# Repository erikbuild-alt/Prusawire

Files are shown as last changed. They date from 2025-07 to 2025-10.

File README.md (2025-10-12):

# Prusawire 2025.B1

Render

A wholly unofficial Prusa MK3 and MK4 total conversion mod, from Positron's April Fools of 2025.

## About

> Nomad of Positron3D came up with this idea shortly after completing their Switchwire build. The idea started as a quick design exercise, to try and convert a Prusa MK4S frame into a Switchwire, using everything left over from a CORE One Upgrade.
>
> As the first iteration wrapped up, I took interest in the project, and decided to take this April Fools joke one step further and build it into a reliable machine.
>
> After months of hard work, please enjoy the build ❤
> 
> [-@ellafoxo](https://www.printables.com/@ellafoxo)

## Who This Printer is For

Pick one of the following:

 - You have an old MK3, MK3S, or MK3S+, and you want to teach an old dog new tricks and are on a budget
 - You upgraded from MK4S to a Core ONE, and have a leftover frame. You are okay spending money on building a new printer with that hardware.

Additionally, the following says this printer is for you: 

 - You want to take your first steps into RepRap beyond Prusa, and Voron is an exciting route.
 - You are comfortable working from a CAD file as your build guide
 - You respect the Frankenstein-y nature of this April Fools joke printer

## Want to Support the Project?

First of all, thank you! Development costs have been mostly self-funded, with filament sponsored by Levendigs, and LDO Motors for providing the funds for the Prusa MK4 frame.

 - Buy me a Ko-Fi
 - Support Positron3D to fund future endeavors

## 2025 - Beta 1

This printer is in active development. Please check back regularly for bug fixes and configuration updates!

## Build Volume

X: 250mm
Y: 210mm
Z: 185mm

## Bill of Materials

[Prusawire 2025.B1 Bill of Materials](BOM/BOM_2025-B1.md)

## Technical Support

Prusawire, technically, does not count as a Voron Switchwire. We ask you kindly not to nag the Voron Design team for technical support.

Instead, please [join the Positron3D Discord](https://discord.com/invite/positron) for support with your build, and maybe share your progress over there too.

## Serial Numbers

We are accepting serials over on the [Positron 3D Discord](https://discord.com/invite/positron). Please submit your request to the #prusawire-serial-request channel over there. 

## Upgrading the Einsy Rambo to Klipper - Read this

Installing Klipper on the Einsy Rambo board is possible, with extra steps. Follow the guide [published by the awesome folks at MyRigs3D](https://myrigs3d.com/blogs/infos/revive-your-prusa-mk3s-with-klipper-1-5-flash-bootloader)! We recommend Method 2.

**Note:** Some users have reported problems using `avrdude` with the latest Raspberry Pi OS version (bookworm). If you experience error messages from avrdude complaining about gpio ports being busy, please try using the bullseye version of Raspberry Pi OS instead, available as "Raspberry Pi OS (Legacy)" in Raspberry Pi Imager.

## Klipper Configuration Files

The most up–to–date Klipper configuration files for setting up or updating the Prusawire are in our [config repository](https://github.com/Positron3D/prusawire-klipper-config).

## Credits 

Many thanks to all the awesome people and companies that have made this possible. Notably:

 - Prusa Research - Cheers, Josef and the team for the MK3/4 platform on which this was built upon!
 - Voron Design - Switchwire
 - Positron 3D Team - Too many to name, you know who you are <3
   - Early development team:
     - Nomad's Galaxy
     - Koosh
     - Birb
 - Jason @ LDO Motors - Part sponsorship
 - Levendigs - Part sponsorship 
 - Early access testers:-
    - Killa_Prints
    - LinksLab
    - Safe
    - Silicon
    - TheNexusAvenger
    - torsten

## Extra Credits for Existing Printed Parts

See the collection for the most up to date! To name them:

 - Printable M3 T-Nuts for 3030 Extrusion, by Kapplion
 - Stealthburner umbilical strain relief, by nagelwerkstatt

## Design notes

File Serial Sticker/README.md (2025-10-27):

Prusawire Serial

Custom serial sticker for Prusawire. Designed for 24 mm tape. Files include a printable cutting stencil.

Brother TZe-M951 Black/Matt Silver tape is tested.

Template files are available as Affinity Designer 2 and Inkscape files.
Used fonts are from [Google Fonts](https://fonts.google.com/specimen/Play). Play in regular and bold.

[Inkscape](https://inkscape.org)

[WEEE symbol](https://europa.eu/youreurope/business/product-requirements/labels-markings/weee-label/index_en.htm)

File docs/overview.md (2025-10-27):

---
layout: default
title: Overview
nav_order: 2
---

# Overview

Welcome to the Prusawire documentation.

## Overview

- [Frequently Asked Questions](faq.html)
- [Bill of Materials](bom.html): Links to all current BOM information.
- [Assembly Manual](assembly-manual.html): Links to the latest Prusawire Assembly Manual PDF.

## Hardware

- [Gantry Deracking](hardware/gantry-deracking.html): How to derack the gantry for smooth and accurate motion.
- [XZ Belt Installation and Tensioning](hardware/xz-belt.html): How to install the main CoreXZ Motion Belts.
- [Y Belt Installation and Tensioning](hardware/y-belt.html): How to install the Y Motion Belt.

## Software
 - [Software Installation Overview](software/index.html)

## Tuning and Calibration
 - [Tuning and Calibration](tuning-calibration/index.html)

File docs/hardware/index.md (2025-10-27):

---
layout: default
title: Hardware Overview
has_children: true
nav_order: 6
---

# Hardware Overview

The official Assembly Manual (along with the Fusion CAD Link) should be your guide for assembly.  There are, of course, a few more complicated procedures which we have documented in detail here:

- Gantry Deracking
- XZ Belt
- Y Belt

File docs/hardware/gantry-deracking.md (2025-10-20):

---
layout: default
title: Gantry Deracking
parent: Hardware Overview
nav_order: 1
---

# Gantry Deracking
{: .no_toc}

<details open markdown="block">
  <summary>
    Table of contents
  </summary>
  {: .text-delta }
- TOC
{:toc}
</details>

**Current Compatibility:** *Prusawire - Beta 1*

## Overview
The gantry de-racking procedure is critical to ensure smooth motion in X and Z.  The general idea is to loosen certain screws on the gantry, bump the bottom of the gantry against the X and Z motor joints to align, and tighten the screws.

## Prerequisites
- Confirm your frame geometry is square: [Frame Assembly - Geometry Check](https://help.prusa3d.com/guide/2-frame-assembly_427481#427929)
- The following should be assembled already:
	- Frame
	- Z-Axis
	- X-Gantry with toolhead mount
- You should be ready to belt both the X and Z axis.

## Instructions
1. Remove the **toolhead** from the **carriage mount** (if currently installed).
	1. For Stealthburner, see the Stealthburner assembly manual for instructions.
2. Remove the **bed**, **y-carriage**, and **y-rods** completely off the printer (if currently installed).
3. Remove the **bumper block** and **door puller block** from the back of the gantry (if currently installed).

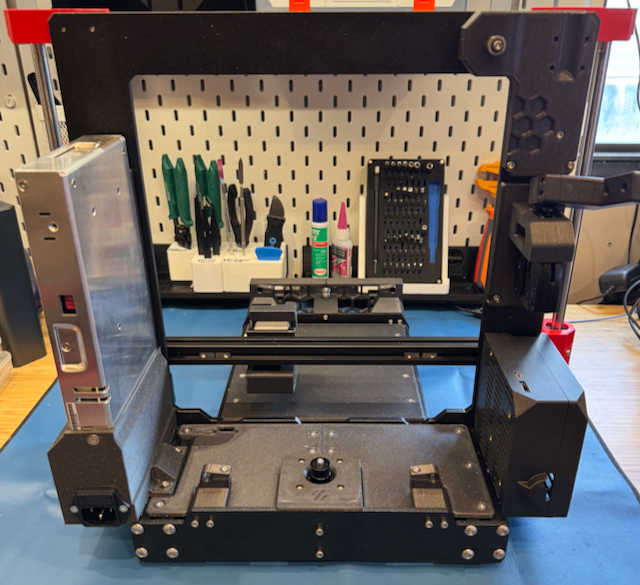
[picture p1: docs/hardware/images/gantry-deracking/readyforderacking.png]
	

4. Remove the **top left idler assembly** and **top right idler assembly** loosening the M3 SHCS on each.  
	1. *TIP: A small piece of tape on the top and bottom of the assembly can be used to help keep the bearing stack together.*

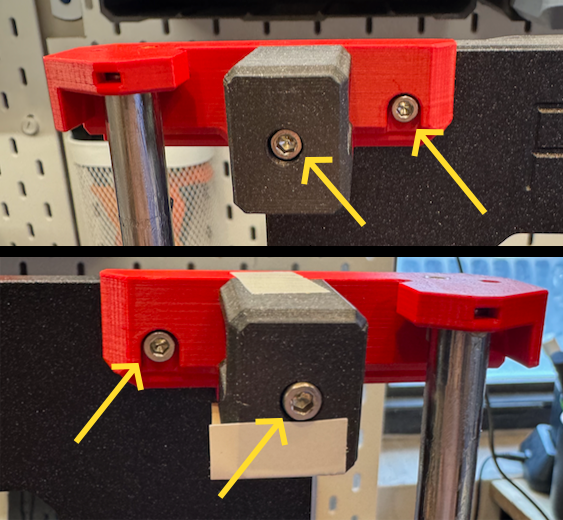
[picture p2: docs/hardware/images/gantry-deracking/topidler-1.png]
	
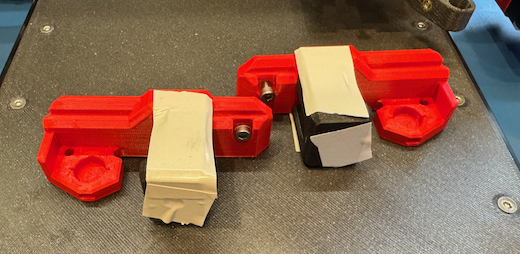
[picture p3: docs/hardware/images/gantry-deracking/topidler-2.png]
	

5. Remove the **x-gantry assembly from the printer** by lifting it up off the z-axis rods.
6. Loosen all six **M5 BHCS** from each side of the x-gantry assembly.

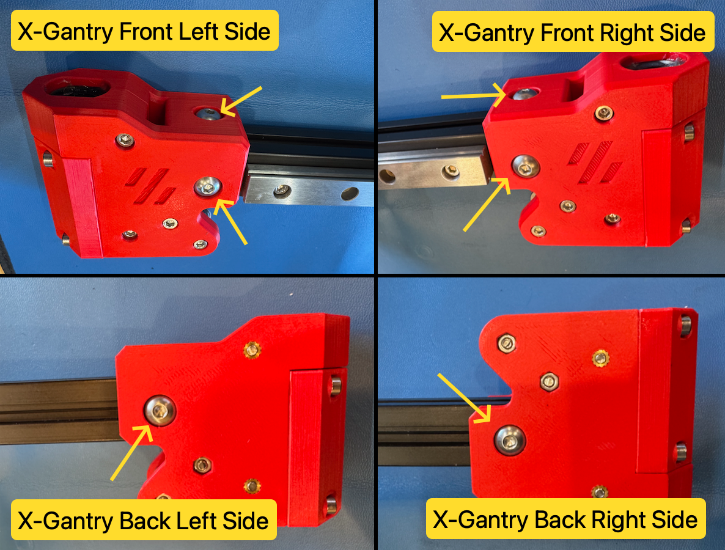
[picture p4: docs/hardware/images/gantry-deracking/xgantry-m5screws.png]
	

7. Ensure each end of the 2020 extrusion is seated ALL the way into the printed parts.
8. Re-install the **x-gantry assembly** onto the printer by sliding it onto the z-axis rods from the top.
9. Move the **x-gantry assembly** up and down a few times to allow parts to settle.
10. Lower the **x-gantry assembly** until it bumps against the X and Z motor mounts.

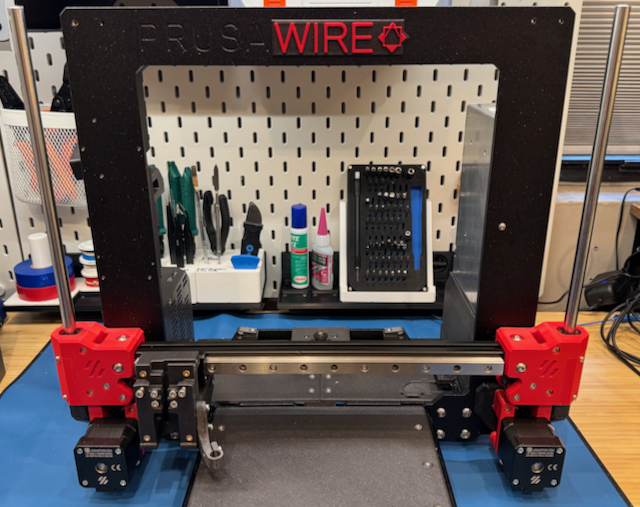
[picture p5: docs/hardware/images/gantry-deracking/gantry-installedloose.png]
	

11. Tighten the two top M5 BHCS on the x-gantry assembly, followed by the two front M5 BHCS.

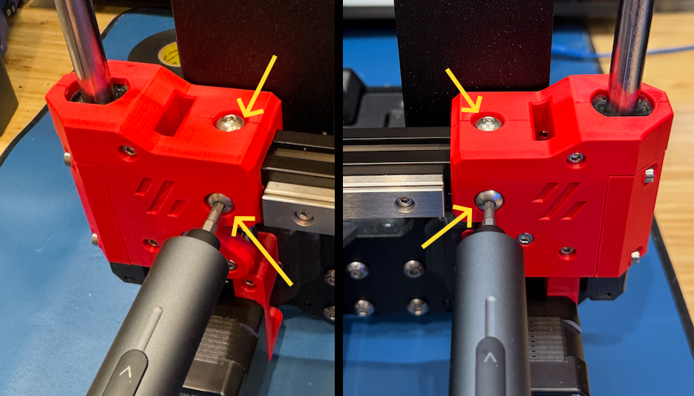
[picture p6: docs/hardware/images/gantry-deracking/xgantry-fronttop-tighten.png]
	

12. Raise the **x-gantry assembly** up to the top just high enough to be able to tighten the rear two M5 BHCS.

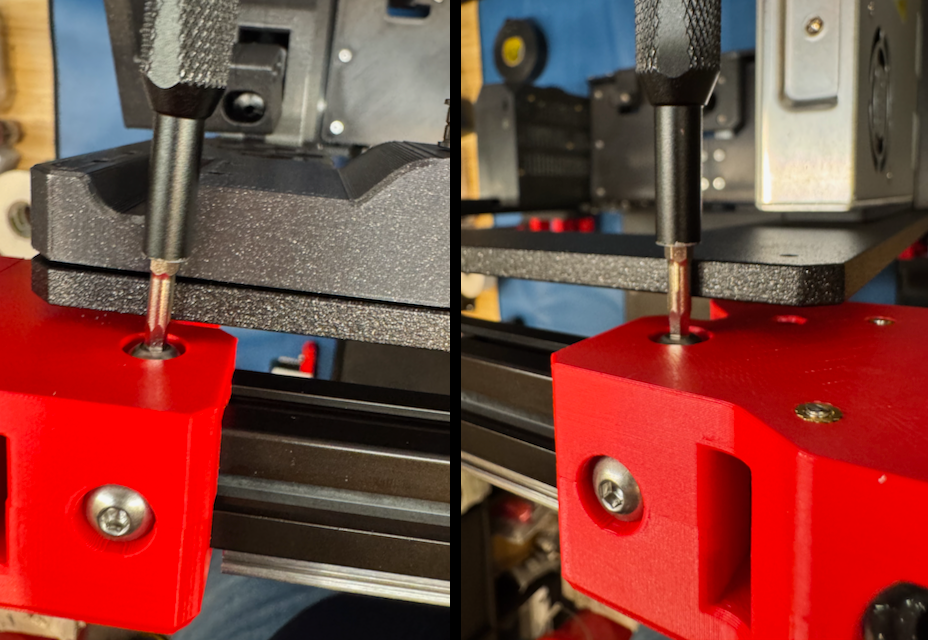
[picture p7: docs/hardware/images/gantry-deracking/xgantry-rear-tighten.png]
	

13. Lower the **x-gantry assembly** back down to the bottom.
14. Re-install the **top left idler assembly** and **top right idler assembly** by tightening the two M3 SHCS on each.
15. Re-install the **bumper block** and **door puller block** on the rear of the gantry.
16. Move the gantry up and down.  You shouldn't feel any resistance.

	

	1. When the gantry bumps the top of the frame, it should bump equally on both sides.

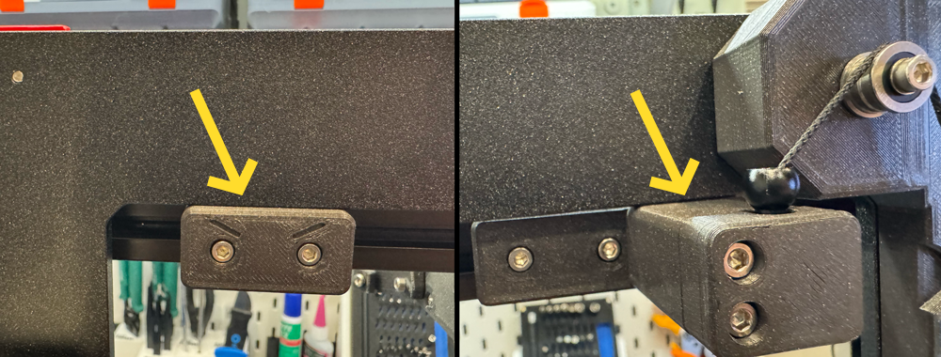
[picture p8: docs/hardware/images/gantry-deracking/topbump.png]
	

	2. When the gantry bumps the bottom (X motor mount and Z motor mount), it should bump equally on both sides.

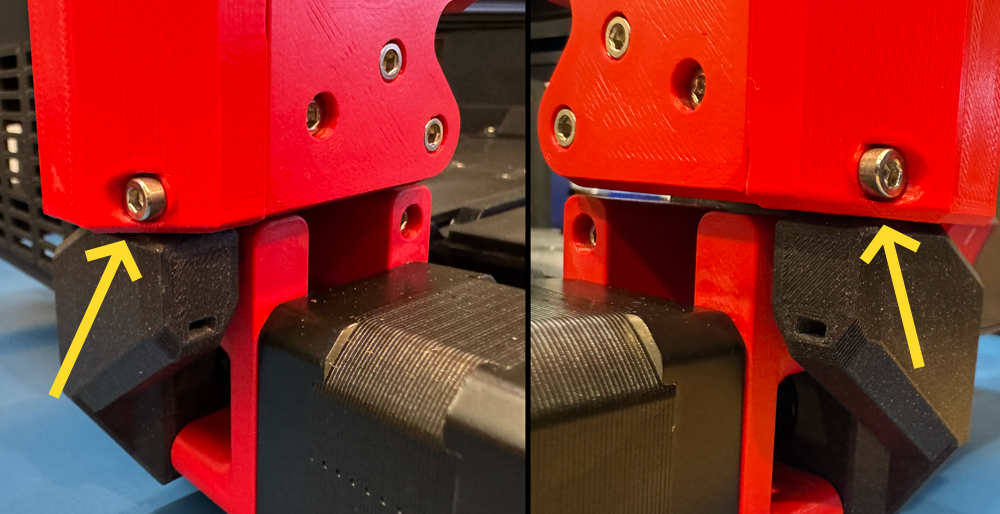
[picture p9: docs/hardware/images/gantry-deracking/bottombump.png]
	

17. Check for any gantry racking a final time after installing XZ belts (and prior to installation of Y-axis).  Adjust front/top M5 screws if needed.

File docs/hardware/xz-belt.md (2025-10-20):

---
layout: default
title: XZ Belt Installation and Tensioning
parent: Hardware Overview
nav_order: 2
---

# XZ Belt Installation and Tensioning
{: .no_toc}

<details open markdown="block">
  <summary>
    Table of contents
  </summary>
  {: .text-delta }
- TOC
{:toc}
</details>

**Compatibility:** *Prusawire - Beta 1*

## Overview
The X and Z belts must be installed and tensioned properly to ensure smooth and accurate gantry motion.

**Important notes:**
- Extra belt length has been specified in the BOM; it is expected to have some leftover belt afterwards.
- Match your belt lengths before assembling the printer!
- When inserting the belt clips, there should be an equal number of teeth sticking out of the ends.
- **DO NOT cut your belts** until you are 1000% certain you have done it correctly.  It's okay to leave a little extra length hanging out the back of the toolhead carriage until final assembly and validation.

## Prerequisites
- Complete the Gantry Deracking procedure.
- Remove the **toolhead** from the **carriage mount** (if currently installed).
	1. For Stealthburner, see the Stealthburner assembly manual for instructions.
- (Optional, but highly recommended) Print and assemble the GT2 Belt Runner to easily and perfectly match your belt lengths: [Belt Runner - GT2 Belt Length Matcher \| Printables.com](https://www.printables.com/model/1192440-belt-runner-gt2-belt-length-matcher)

## Instructions 
### Belt Installation
1. Measure out 1600mm of GT2 belt for the X axis.  Double-check your measurement, then cut this length.  Set aside for now.
	- *Tip: Mark some tape on your desk with 100mm increments using a tape measure or calipers.*

	

2. Measure out another ~1600mm length of GT2 belt for the Z axis.  **Do not cut it yet!**
3. Match the belt lengths (*note: if not using the GT2 Belt Runner, carefully match the belt lengths by hand!*)
	1. Align the starting teeth of the of the X belt and Z belt.  
	2. Feed into the GT2 Belt Runner (see above).  
	3. Use belt runner to find the exact same length of Z belt as X belt.  Note one belt will be exactly one tooth offset from the other.  
	4. Once you are sure the belts are the same length, cut the **Z belt** to match the **X belt**.

	
	
4. Using tape or a zip tie, raise the gantry about 75% of the way towards the top of the frame.

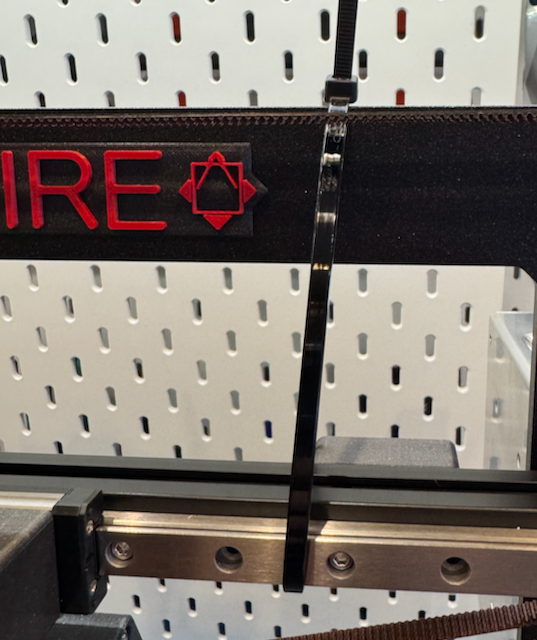
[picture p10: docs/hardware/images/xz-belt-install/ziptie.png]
	
	
5. Remove the 4x **M3x14 SHCS** securing the **x carriage assembly** to the linear rail.  Remove the assembly.
	
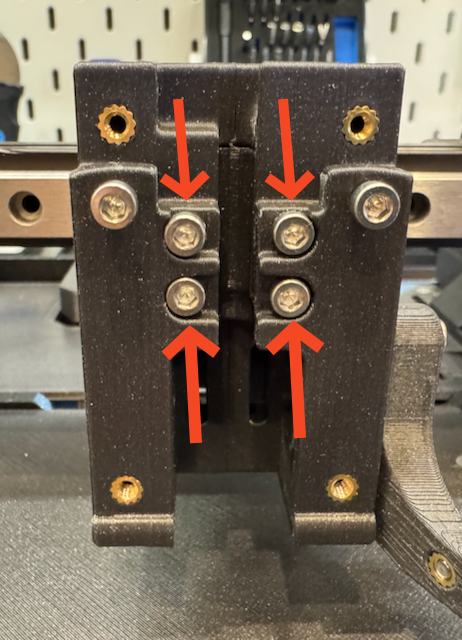
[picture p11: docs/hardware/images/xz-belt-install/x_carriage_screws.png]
	

6. Remove the 3x **M3x40 SHCS** from the left side of the **x-carriage assembly** to separate the left side from the right side.
	
	

7. Gather all the needed parts:
	- 2x **1600mm Gates GT2 Belt**
	- 2x **M3x40 SHCS**
	- 2x **\[a]_belt_tensioner_clip**
	- 2x **\[a]_belt_clip**
	- 2x **belt_clip**
	- 4x **M3x14 SHCS**
	- 1x **x-carriage - left side**
	- 1x **x-carriage - right side**

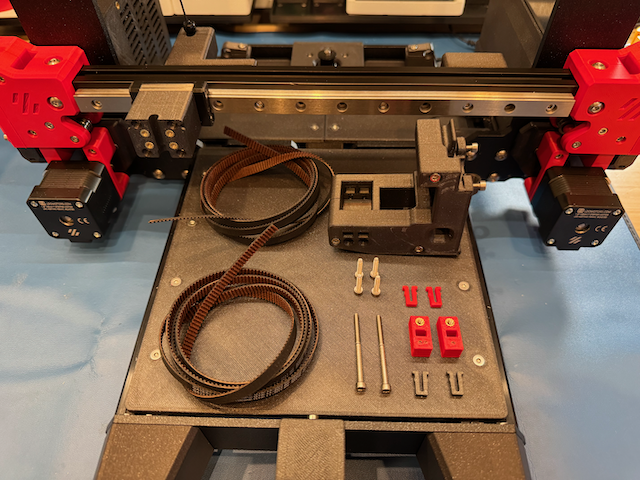
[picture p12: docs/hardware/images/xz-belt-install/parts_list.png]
	
    
8. Take the **x-carriage - right side** and install it back onto the **x-carriage mount** (on the rail) with 2x **M3x14 SHCS**.
9. Take the first **\[a]_belt_tensioner_clip**.  Feed a small amount of one of the belts (belt teeth facing up) through the slot on the side with the heat insert.  Pass just enough belt through so 3 teeth are visible from the opposite side.  Insert a **belt_clip** under to secure.
	- *Tip: You can press the retaining clip against a flat surface to help force the retaining clip into the tensioner clip.*
    
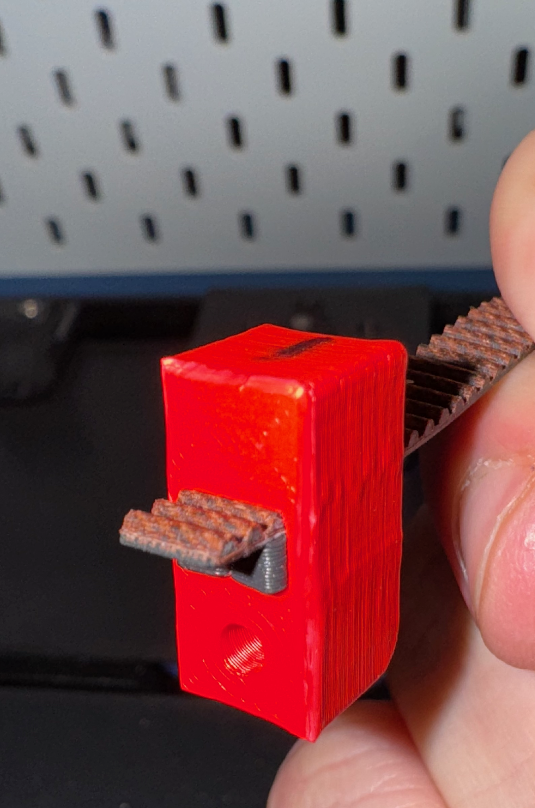
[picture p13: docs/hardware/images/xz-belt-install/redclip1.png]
	
	

10. Repeat this process for the other clip and belt.  It is critical for both clips to have the same number of exposed belt teeth showing.
11. Pass the long end of each belt (teeth facing up) through the two slots from the inside to the outside of the mounted **x-carriage - right side**.
	- *NOTE: The **\[a]_belt_tensioner_clip** with the single dot goes towards the rear of the printer.  The clip with the two dots goes towards the front of the printer.

	
	

12. **Z Belt**: Route the belt through the belt path (see diagram; belt path noted in GREEN):
	1. Right towards the **XZ Block - Right**.
	2. Around the bearing stack and down towards the **Z Motor**.
	3. Back up around the **Z Motor Pulley** through the **XZ Block - Right** towards the **Idler Block - Right**.
	4. Around the bearing stack and left towards **Idler Block - Left**.
	5. Around the bearing stack and down towards **XZ Block - Left**.
	6. Around the bearing stack and right towards the **X-carriage**.
	7. *Tip: Make sure the belt isn't twisted at any point!*
	8. *Tip: Check the Z Motor Pulley alignment with the belt.  Adjust with the set screws on the pulley if needed to ensure good belt alignment that doesn't rub on the motor mounts.*

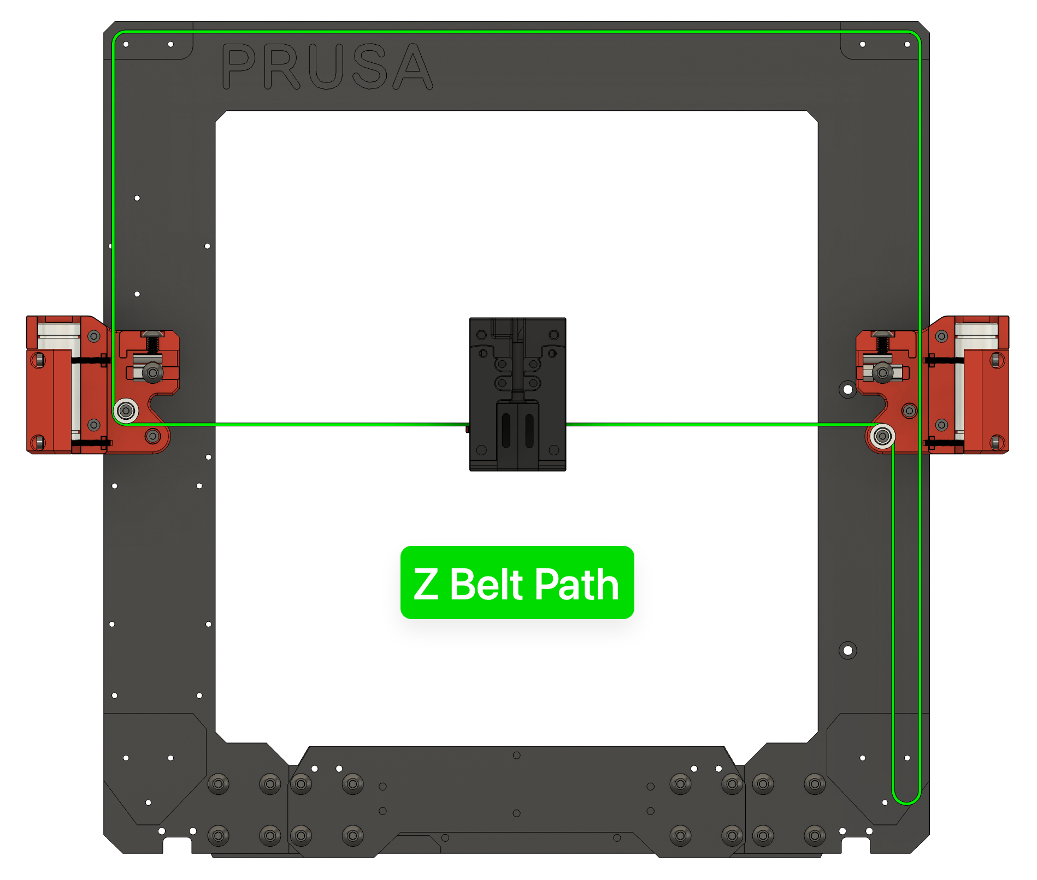
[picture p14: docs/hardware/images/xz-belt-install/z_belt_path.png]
	
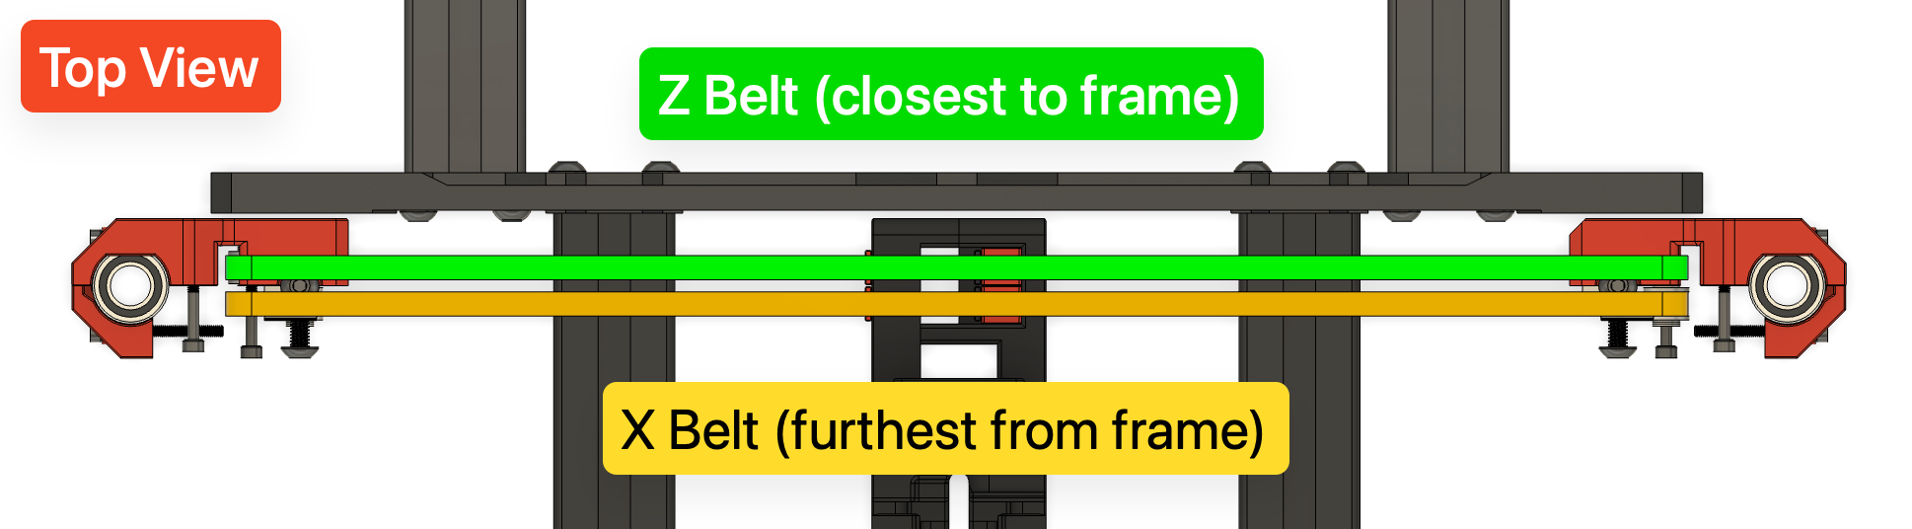
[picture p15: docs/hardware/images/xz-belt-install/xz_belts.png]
	

13. **X Belt**: Route the belt through the belt path (see diagram; belt path noted in YELLOW):
	1. Right towards the **XZ Block - Right**.
	2. Around the bearing stack and up towards **Idler Block - Right**.
	3. Around the bearing stack and left towards **Idler Block - Left**.
	4. Around the bearing stack and down through **XZ Block - Left** towards **X Motor**.
	5. Back up around the **X Motor Pulley** towards **XZ Block - Left**.
	6. Around the bearing block and right towards the **x-carriage**.
	7. *Tip: Make sure the belt isn't twisted at any point!*
	8. *Tip: Check the X Motor Pulley alignment with the belt.  Adjust with the set screws on the pulley if needed to ensure good belt alignment that doesn't rub on the motor mounts.*

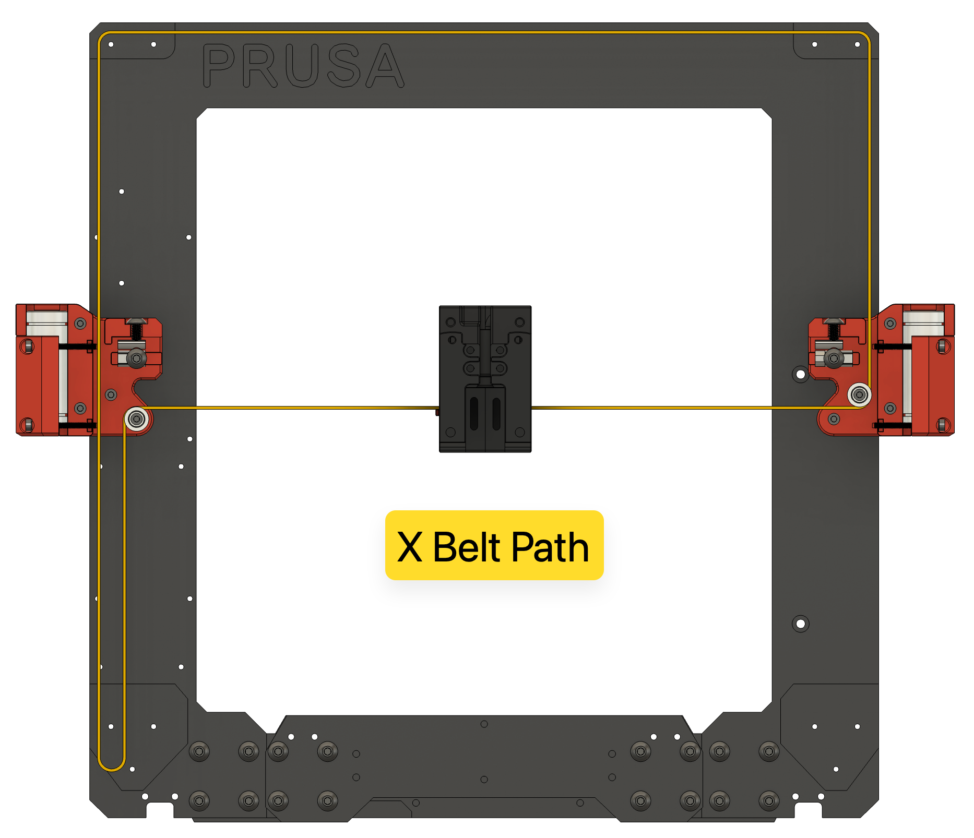
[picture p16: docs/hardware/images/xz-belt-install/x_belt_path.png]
	

14. Pass the two belts through the outside of the **x-carriage - left side**.  
	
	

15. Rejoin the **x-carriage - left side** to the mounted carriage with the 3x **M3x40 SHCS**.  Direct the excess belt length down for now.

	

16. Pull the excess belts evenly to remove the slack from the belt system.  Carefully line up the ends of the belts to ensure they are the same length and the ends match up evenly.
17. Insert both **\[a]_belt_clips** to secure the belts to the left side of the carriage.

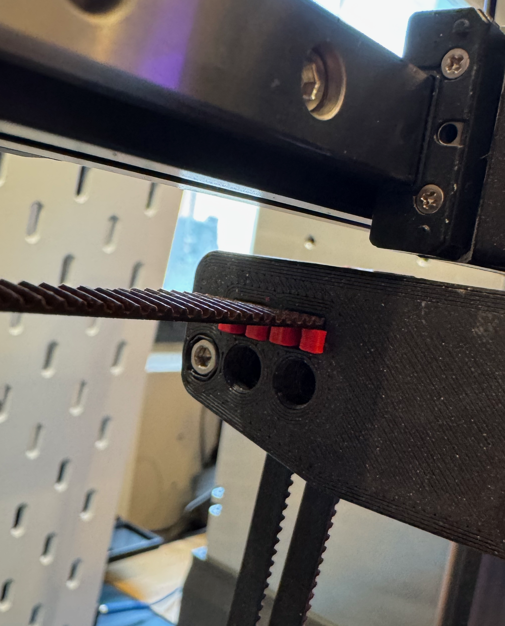
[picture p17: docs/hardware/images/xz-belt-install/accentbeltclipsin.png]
	

18. Confirm once again the ends of the belts are perfectly aligned.  If they have shifted, remove the clips and re-adjust.
19. Unmount the **x-carriage assembly** from the linear rail one last time by removing the 2x **M3x14 SHCS** from the front.
20. Carefully rotate the assembly towards you to view the belts inside.

	

21. Leaving 3 to 4 teeth exposed on the left side of the assembly, carefully cut the belts.

	

22. Re-mount the assembly back onto the linear rail carriage with all 4x **M3x14 SHCS**.
23. Install the 2x **M3 x 40 SHCS** into the left side of the **x-carriage assembly** and screw into the **\[a]_belt_tensioner_clips** until just seated.
	
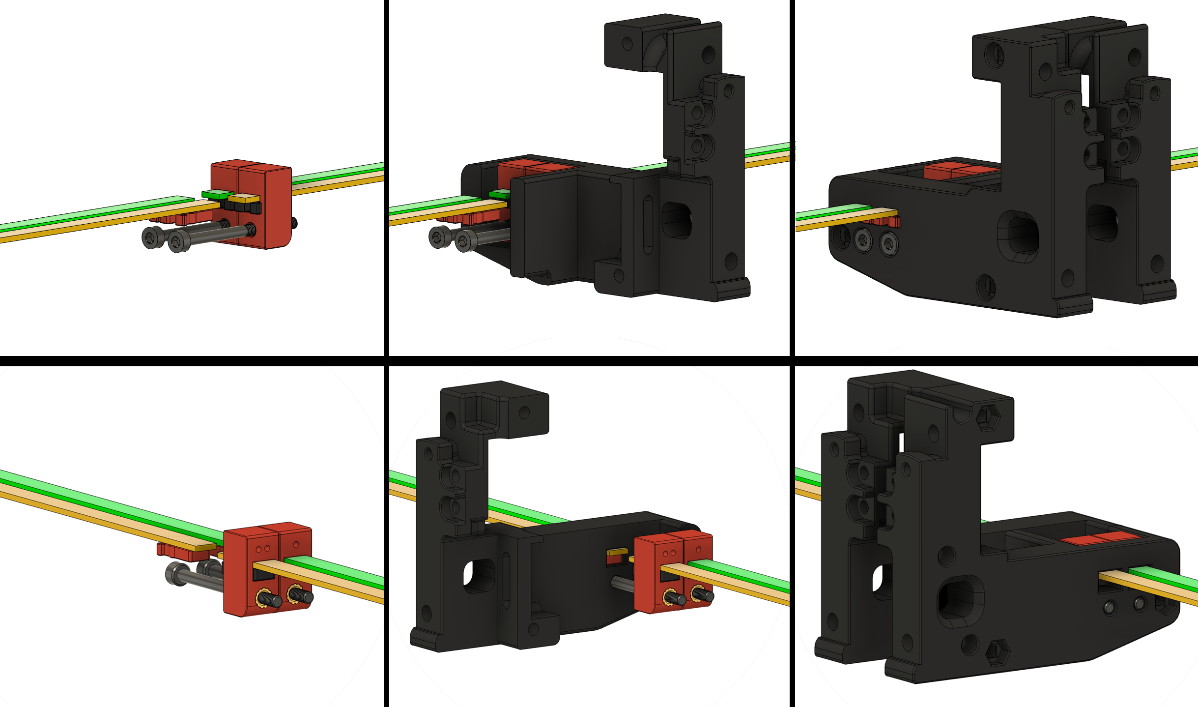
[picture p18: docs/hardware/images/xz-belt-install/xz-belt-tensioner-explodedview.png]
	

24. You are finished and ready to tension the XZ Belts!

	

### Belt Tensioning
To properly tension the X and Z belts:
1. Begin turning the two **M3x40 SHCS tensioning screws** in the **x-carriage assembly**.
	- Turn clockwise to increase tension.
	- Turn counterclockwise to decrease tension.
2. Once slack is removed, and prior to final tension:
	- **TRIPLE CHECK YOUR BELTS to make sure they are riding correctly on the bearings and pulleys.  If they aren't, loosen and correct.**
3. If the tensioning screw bottoms out you can either:
	- Replace the M3x40 SHCS with a fully threaded version
	- Try tensioning both belts a few more groove notches on the left side of the **x-carriage assembly** and re-installing the **\[a]_belt_tensioner_clips** to secure.

4. Visually inspect your X carriage belt tensioner. If your belts are not stretched, you should see that the two tensioner blocks are almost in line with one another. 
	
	
    
5. Come to the front of the printer and inspect the right side of your X carriage. Your belt teeth should align with one another. If they do not, make minor adjustments to the tensioner screws until they do.
	
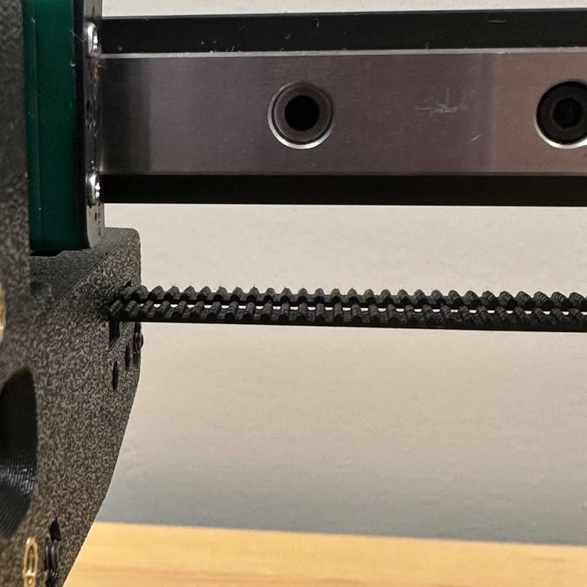
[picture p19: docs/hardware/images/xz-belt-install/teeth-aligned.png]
	

6. Follow up with tuning your belt tension with one of the final tensioning options below.

**Final Tensioning Options:**
- **PF Makes Belt Tensioning Meter:** [3D-Printer/GT2 Belt Tension Meter at main · Diyshift/3D-Printer · GitHub](https://github.com/Diyshift/3D-Printer/tree/main/GT2%20Belt%20Tension%20Meter)
	- Switchwire "Z" Spec - 1.8 to 2.2 (1.9 to 2.3 for EPDM high-temp belt)
- **Prusa Belt Tension Gauge:** [Tension Meter for the GT2 belts of i3 MK3S+ or Prusa MINI+ by Prusament \| Download free STL model \| Printables.com](https://www.printables.com/model/46639-tension-meter-for-the-gt2-belts-of-i3-mk3s-or-prus)
- **Biqu's Digital Belt Tension Tool:** [GitHub - bigtreetech/Belter-belt-tension-Tool: Belter belt tension Tool Info Page](https://github.com/bigtreetech/Belter-belt-tension-Tool)
- **Prusa Mobile App:** 
	- [Prusa on the Apple App Store](https://apps.apple.com/us/app/prusa/id6477531937)
	- [Prusa - Apps on Google Play](https://play.google.com/store/apps/details?id=com.prusa3d.connect&hl=en-US&pli=1)
	- Tuner Mode for *MK3S --> X-Axis*
		- Carriage all the way to the right
- **Prusa Website Tuner:** [Prusa Belt tuner](https://belt.connect.prusa3d.com/)
	- *MK3S --> X-Axis*
		- Carriage all the way to the right
- **Gates Carbon Drive Mobile App**
	- [Carbon Drive Belt Tension Tool on the Apple App Store](https://apps.apple.com/app/bicycle-belt-tension-meter/id438346486)
	- [Carbon Drive - Apps on Google Play](https://play.google.com/store/apps/details?id=com.gates.carbondrivecalculator&hl=en)
	- 85 Hz

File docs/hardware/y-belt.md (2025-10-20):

---
layout: default
title: Y Belt Installation and Tensioning
parent: Hardware Overview
nav_order: 2
---

# Y Belt Installation and Tensioning
{: .no_toc}

<details open markdown="block">
  <summary>
    Table of contents
  </summary>
  {: .text-delta }
- TOC
{:toc}
</details>

**Compatibility:** *Prusawire - Beta 1*

## Overview
The Y belt must be installed and tensioned properly to ensure smooth and accurate bed motion.

**Important notes:**
- Extra belt length has been specified in the BOM; it is expected to have some leftover belt afterwards.
- **DO NOT cut your belts** until you are 1000% certain you have done it correctly.  It's okay to leave a little extra length hanging out until final assembly and validation.

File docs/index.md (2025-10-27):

---
layout: default
title: Home
nav_order: 1
---

# Positron3D's Prusawire Documentation

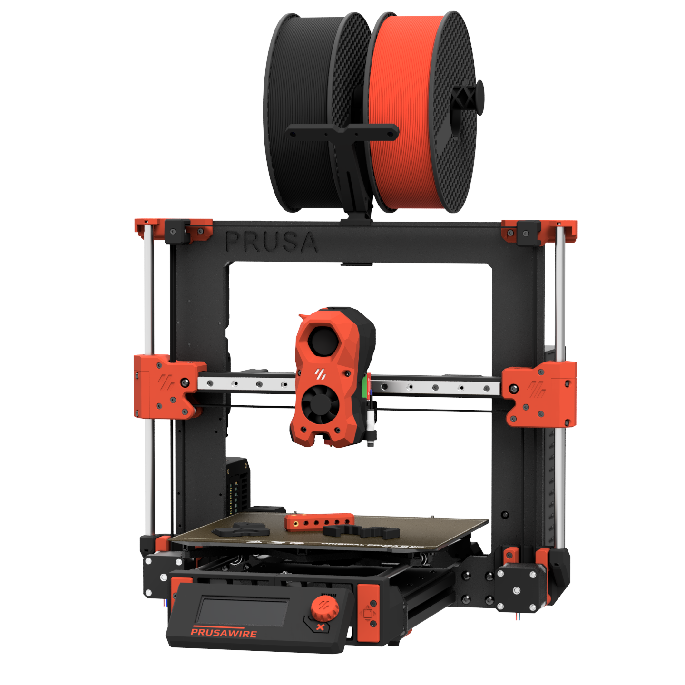
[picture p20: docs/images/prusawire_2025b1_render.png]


A wholly unofficial Prusa MK3 and MK4 to Switchwire total conversion mod, from Positron's April Fools of 2025.

## About

> Nomad of Positron3D came up with this idea shortly after completing their Switchwire build. The idea started as a quick design exercise, to try and convert a Prusa MK4S frame into a Switchwire, using everything left over from a CORE One Upgrade.
>
> As the first iteration wrapped up, I took interest in the project, and decided to take this April Fools joke one step further and build it into a reliable machine.
>
> After months of hard work, please enjoy the build ❤
> 
> [-@ellafoxo](https://www.printables.com/@ellafoxo)

## Who This Printer is For

Pick one of the following:

 - You have an old MK3, MK3S, or MK3S+, and you want to teach an old dog new tricks and are on a budget
 - You upgraded from MK4S to a Core ONE, and have a leftover frame. You are okay spending money on building a new printer with that hardware.

Additionally, the following says this printer is for you: 

 - You want to take your first steps into RepRap beyond Prusa, and Voron is an exciting route.

## Technical Support

Prusawire, technically, does not count as a Voron Switchwire. We ask you kindly not to nag the Voron Design team for technical support.

Instead, please [join the Positron3D Discord](https://discord.com/invite/positron) for support with your build, and maybe share your progress over there too.

## Serial Numbers

We are accepting serials over on the [Positron 3D Discord](https://discord.com/invite/positron). Please submit your request to the #prusawire-serial-request channel over there.

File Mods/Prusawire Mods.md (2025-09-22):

# Prusawire Mods

*This is a non-exhaustive collection of Prusawire Mods. Many of these were created for Beta 1.*

## Electronics
- [Prusawire MMU LCD Cover with insert letters by @einarjh](https://www.printables.com/model/1392274-prusawire-mmu-lcd-cover-with-inset-letters)
- [BTT PI TFT50 V2.1 Prusawire Housing by @telefaksi](https://www.printables.com/model/1384689-btt-pi-tft50-v21-prusawire-housing)
- [Prusawire BigTreeTech HDMI 5 Mount by @TheNexusAvenger](https://www.printables.com/model/1377302-prusawire-bigtreetech-hdmi-5-mount)
- [Prusawire ELectronics Tower by @TheNexusAvenger](https://www.printables.com/model/1415732-prusawire-electronics-tower)
- [Prusawire Cable Management Mods by @telefaksi](https://www.printables.com/model/1374187-prusawire-cable-management-mods)
- [Prusawire Cable Management - Additional Mods by @erikbuild](https://www.printables.com/model/1422355-prusawire-cable-management-additional-mods)

## Power Supplies
- [Meanwell LRS-350 / RSP-320 PSU Mount by @erikbuild](https://www.printables.com/model/1386144-meanwell-lrs-350-24-rsp-320-24-psu-mount-for-prusa)

## Decking / Panels
- [Prusawire Deck Panel for Countersunk Screws by @Safe](https://www.printables.com/model/1374282-prusawire-deck-panel-for-countersunk-screws)
- [Prusawire Beta 1 - Rear Deck Cover Plate by @erikbuild](https://www.printables.com/model/1384528-prusawire-rear-deck-cover-plate)

## Frame and Motion
- [8mm to 10mm Bushings for Prusawire by @Safe](https://www.printables.com/model/1369871-8mm-to-10mm-bushings-for-prusawire)
- [Prusawire Key-Bak Mounting Bracket by @telefaksi](https://www.printables.com/model/1371269-prusawire-key-bak-mounting-bracket)

## Aesthetics
- [Prusawire Supplemental Badge by @TheNexusAvenger](https://www.printables.com/model/1368495-prusawire-supplemental-badge)

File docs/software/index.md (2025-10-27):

---
layout: default
title: Software Overview
has_children: true
nav_order: 7
---

# Software Overview

## Klipper Configuration Files

The most up–to–date Klipper configuration files for setting up or updating the Prusawire are in our [config repository](https://github.com/Positron3D/prusawire-klipper-config).

## Upgrading the Einsy Rambo to Klipper - Read this

Installing Klipper on the Einsy Rambo board is possible, with extra steps. Follow the guide [published by the awesome folks at MyRigs3D](https://myrigs3d.com/blogs/infos/revive-your-prusa-mk3s-with-klipper-1-5-flash-bootloader)! We recommend Method 2.

**Note:** Some users have reported problems using `avrdude` with the latest Raspberry Pi OS version (bookworm). If you experience error messages from avrdude complaining about gpio ports being busy, please try using the bullseye version of Raspberry Pi OS instead, available as "Raspberry Pi OS (Legacy)" in Raspberry Pi Imager.

## Resources
- [Voron Software Installation Guide](https://docs.vorondesign.com/build/software/) for some good resources on Mainsail (Klipper on Raspberry Pi) and Control Board firmware.
- [Raspberry Pi OS based \| MainsailOS](https://docs-os.mainsail.xyz/getting-started/raspberry-pi-os-based)
- [Welcome to Mainsail \| Mainsail](https://docs.mainsail.xyz/)
- [GitHub - bigtreetech/BIGTREETECH-SKR-mini-E3](https://github.com/bigtreetech/BIGTREETECH-SKR-mini-E3)
- [BIGTREETECH-SKR-mini-E3/firmware/V3.0/Klipper at master · bigtreetech/BIGTREETECH-SKR-mini-E3 · GitHub](https://github.com/bigtreetech/BIGTREETECH-SKR-mini-E3/tree/master/firmware/V3.0/Klipper)

## Configuration
Start with the [Positron3D Prusawire Configuration](https://github.com/Positron3D/prusawire-klipper-config) settings and profiles.

More detail general instructions are found at [Software Configuration \| Voron Documentation](https://docs.vorondesign.com/build/software/configuration.html).

### Sensorless Homing
If you are running the Einsy board, congrats, you are now done.

For the BTT SKR Mini E3, some further tuning likely needs to happen. Refer to [this guide](https://gist.github.com/clee/9108f7717defce8b1222698f816def0a#finding-the-right-stallguard-threshold) by clee on setting the correct stallguard threshold.
### Input Shaper
Some defaults have been provided, but they are no doubt unsuitable for your exact machine. We recommend installing [ShakeTune](https://github.com/Frix-x/klippain-shaketune) for measuring resonances, and reading the [Klipper guide](https://www.klipper3d.org/Measuring_Resonances.html#max-smoothing) on understanding which value to choose.

**Y Axis Input Shaping**: This requires an external accelerometer (eg LDO Input Shaper) to be mounted to your heated bed.

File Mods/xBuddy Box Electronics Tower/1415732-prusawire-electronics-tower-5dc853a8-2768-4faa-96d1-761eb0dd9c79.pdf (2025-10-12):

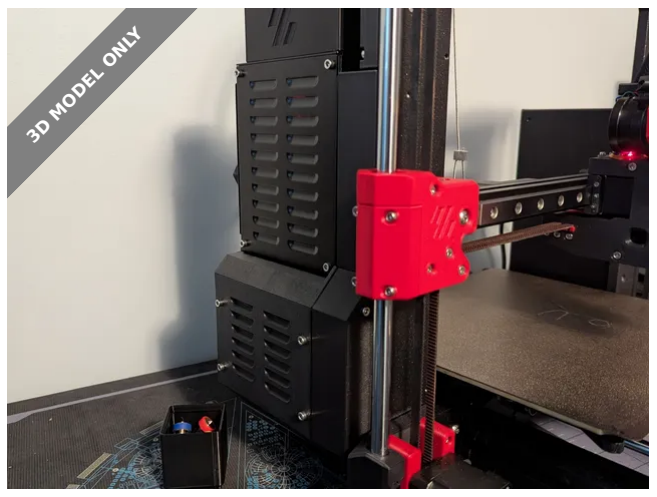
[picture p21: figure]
3D MODEL ONLY

# Summary

Electronics mount for the Prusawire using the xBuddy board electronics box from the Prusa MK4.

3D Printers (https://printables.com/model?categoryId=1) > Prusa Parts & Upgrades (https://printables.com/model?categoryId=134)

Tags: | prusa | mk4 | switchwire | mk4s | prusawire

The stock Prusawire puts most of the electronics on the bottom and does not re-use the xBuddy box used on the MK3.5, MK3.9, and MK4. This alternative mount option bundles all of the following hardware in a tower meant to mimic the MK4 design:

Door puller
MCU (BTT SKR Mini provided, please remix for others)
Raspberry Pi
24V to 5V DC buck converter
WAGO 221-413s
(Optional) USB hub

There is also a 1x2 Gridfinity mount at the top of the optional cable holder (for LDO Nitehawk). The USB ports and networking are all accessible from the back of the tower.

TheNexusAvenger (https://printables.com/@TheNexusAvenger)

# Prusawire Electronics Tower

VIEW IN BROWSER (https://printables.com/model/1415732-prusawire-electronics-tower)

updated 15. 9. 2025 | published 15. 9. 2025

•
•
•
•
•
•

# Model files

See the GitHub repository for printing and assembly. (https://github.com/TheNexusAvenger/Prusawire-Electronics-Tower) Some parts are mutually exclusive (as in, if 1 is printed, the other shouldn't) -make sure to read the bill of materials before printing.

# This remix is based on

Prusawire 2025.B1 (BETA 1) (https://printables.com/model/1363547-prusawire-2025b1-beta-1) by Ella Fox (https://printables.com/@ellafoxo)

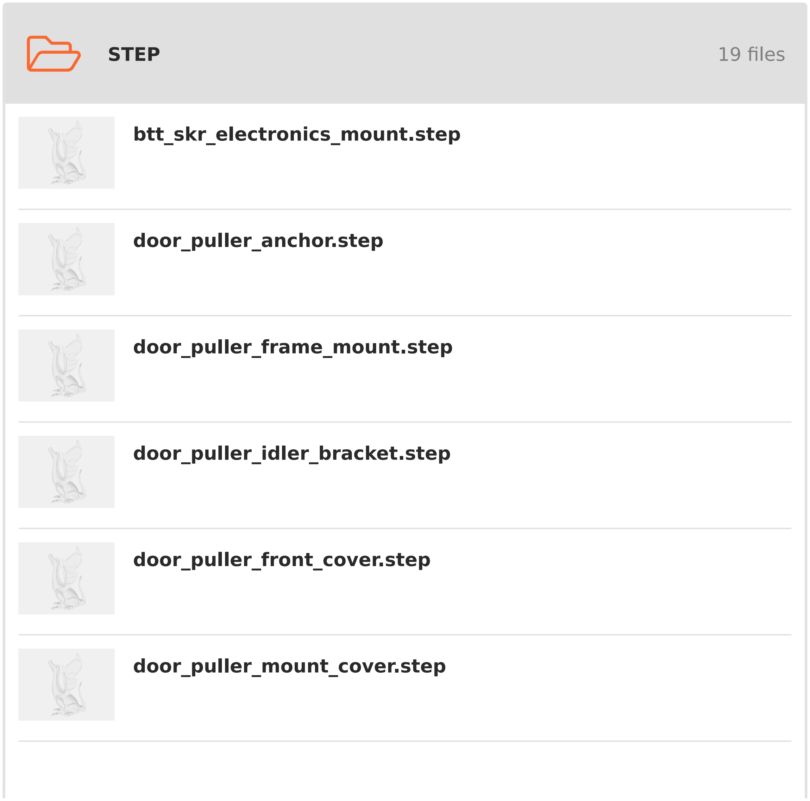
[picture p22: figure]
STEP; 19 files; btt_skr_electronics_mount.step; door_puller_anchor.step; door_puller_frame_mount.step; door_puller_idler_bracket.step; door_puller_front_cover.step; door_puller_mount_cover.step

electronics_box_top_cover_simple.step

electronics_top_cable_cover_gridfinity.step

electronics_top_cable_holder.step

heatbed_cable_holder.step

ldo_nitehawk_usb_board_holder.step

lower_electronics_bottom_cover.step

lower_electronics_main_cover.step

lower_electronics_raspberry_pi_back_wall.step

lower_electronics_raspberry_pi_base_wall.step

lower_electronics_top_cover.step

upper_frame_mount.step

wago_221-413_mount.step

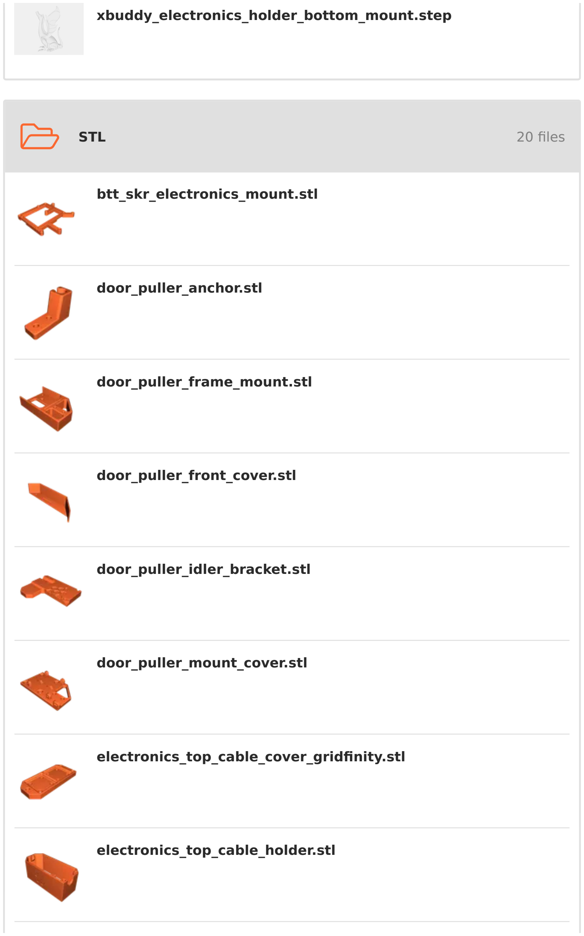
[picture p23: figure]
STL; 20 files; xbuddy_electronics_holder_bottom_mount.step; btt_skr_electronics_mount.stl; door_puller_anchor.stl; door_puller_frame_mount.stl; door_puller_front_cover.stl; door_puller_idler_bracket.stl; door_puller_mount_cover.stl; electronics_top_cable_cover_gridfinity.stl; electronics_top_cable_holder.stl

electronics_box_top_cover_simple.stl

heatbed_cable_holder.stl

ldo_nitehawk_usb_board_holder.stl

lower_electronics_bottom_cover.stl

lower_electronics_main_cover.stl

lower_electronics_raspberry_pi_back_wall.stl

lower_electronics_raspberry_pi_base_wall_reduced_lo… .stl

lower_electronics_top_cover.stl

upper_frame_mount.stl

wago_221-413_mount.stl

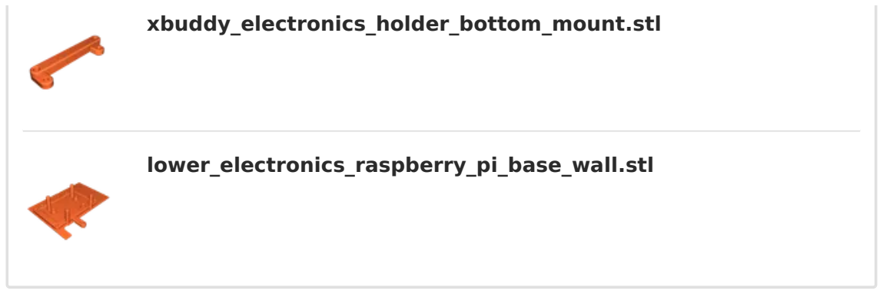
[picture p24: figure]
xbuddy_electronics_holder_bottom_mount.stl; lower_electronics_raspberry_pi_base_wall.stl

# License

This work is licensed under a GNU

General Public License v3.0 (https://www.gnu.org/licenses/gpl-3.0.html)

✖ | Sharing without ATTRIBUTION
✔ | Remix Culture allowed
✔ | Commercial Use
✔ | Meets Open Definition
ℹ | Share under the same license

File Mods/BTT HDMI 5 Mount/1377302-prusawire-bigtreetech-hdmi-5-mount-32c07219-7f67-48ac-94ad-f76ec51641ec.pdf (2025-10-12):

3D MODEL ONLY

## Summary

BigTreeTech HDMI 5 mount for the Prusawire.

3D Printers (https://printables.com/model?categoryId=1) > Prusa Parts & Upgrades (https://printables.com/model?categoryId=134)

Tags: | prusa | voron | switchwire | prusawire

This is an alternative mount for the Prusawire to use with the
BIGTREETECH HDMI5 V1.2. (https://biqu.equipment/products/bigtreetech-hdmi5-v1-0-hdmi7-v1-0) Most frames for the display should work, but only this remix was tested. (https://www.printables.com/model/1377298-bigtreetech-hdmi5-display-voron-mount-v12-version) This is untested on V1.1 and older.

No changes to the mounting screws to the frame from the Prusawire or the screws to the BTT HDMI5 are needed, but 4 “Voron spec” heat set inserts (https://cnckitchen.store/products/made-for-voron-gewindeeinsatz-threaded-insert-m3x5x4-100-stk-pcs) are required (2 per part on the back side facing the Prusawire frame). The mounts are symmetrical, so only one side is provided with the other one requires being mirrored in the slicer.

As shown, black Polymaker ASA (https://us.polymaker.com/products/polylite-asa) was used. “Voron spec” print parameters were used (4 perimeters, 40% infill, 5 top and bottom layers, 0.2mm layer height), although all can probably be changed without any side effects as long as the screen is not grabbed for lifting.

TheNexusAvenger (https://printables.com/@TheNexusAvenger)

## Prusawire BigTreeTech HDMI 5 Mount

VIEW IN BROWSER (https://printables.com/model/1377302-prusawire-bigtreetech-hdmi-5-mount)

updated 6. 8. 2025 | published 6. 8. 2025

## Model files

## This remix is based on

Prusawire 2025.B1 (BETA 1) (https://printables.com/model/1363547-prusawire-2025b1-beta-1) by Ella Fox (https://printables.com/@ellafoxo)

- Print 2, with 1 mirrored on the X or Y axis.
- Print 2, with 1 mirrored on the X or Y axis.

## License

This work is licensed under a GNU

General Public License v3.0 (https://www.gnu.org/licenses/gpl-3.0.html)

✖ | Sharing without ATTRIBUTION
✔ | Remix Culture allowed
✔ | Commercial Use
✔ | Meets Open Definition
ℹ | Share under the same license btt-hdmi-5-prusawire-mount.stl

btt-hdmi-5-prusawire-mount.step

btt-hdmi-5-prusawire-mount.f3d

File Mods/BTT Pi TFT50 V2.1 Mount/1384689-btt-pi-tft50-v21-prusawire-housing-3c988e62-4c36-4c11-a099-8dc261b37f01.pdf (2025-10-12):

3D MODEL ONLY

## Summary

BTT PI TFT50 V2.1 housing for Prusawire in Prusa-style design.

3D Printers (https://printables.com/model?categoryId=1) > Prusa Parts & Upgrades (https://printables.com/model?categoryId=134)

Tags: | btttft50 | prusawire

FOR BTT PI TFT50 V2.1!

Print instructions

Cover, back plate and supports can be printed from ASA, ABS, PETG, PLA or any other suitable material. Buttons are highly recommended to be printed from PETG or other flexible material. No supports needed :)

Print also the included modified front_grill_left part that has hole for DSI-cable to go through.

I printed mine from Prusament ASA (galaxy black, Prusa orange and signal white), Fillamentum ASA white aluminium and Prusament PETG galaxy black.
Required hardware

7 pcs M3x8 BHCS

telefaksi (https://printables.com/@telefaksi_1298577)

## BTT PI TFT50 V2.1 Prusawire housing

VIEW IN BROWSER (https://printables.com/model/1384689-btt-pi-tft50-v21-prusawire-housing)

updated 15. 8. 2025 | published 15. 8. 2025

•

2 pcs M3x6 BHCS
12 pcs M3 Threaded Insert - M3x5x4 (Voron spec)
1 pc M3 square nut
4 pcs display mounting screws that come with the display
Assembly instructions

Preparing the right support


Insert 4 threaded inserts, circled with yellow.

•
•
•
•

Preparing the left support

Insert 4 threaded inserts, circled with yellow. Insert 1 square nut, circled with green.


Fix the two halves of the left support together with M3x6 BHCS, circled with yellow. This is also good point to insert DSI-cable inside the support but it can be pushed through afterwards.

Preparing the back plate

IMPORTANT! Insert M3x6 BHCS (red circle) before installing the left support as the screw can't be inserted after the support is in place. Note also that it is inserted from other side compared to support mounting screws (yellow circle).

Mounting the supports

Fix the supports in place with 4 M3x8 BHCS (yellow circle) and double check that you remembered to insert one M3x6 BHCS in the previous step (red circle).

Mounting BTT PI TFT50 V2.1

Connect the DSI cable to the display and fix the display to the back plate with 4 screws that came with the display (yellow circle).

Preparing the cover

Insert 4 threaded inserts, circled with yellow. Slide the buttons in to the slot in the cover (green circle).

Mounting the cover

Fix the cover in place with three M3x8 BHCS (yellow circle) and tighten the previously inserted M3x6 BHCS (dashed red circle).

Haribo time!

## This remix is based on

Prusawire 2025.B1 (BETA 1) (https://printables.com/model/1363547-prusawire-2025b1-beta-1) by Ella Fox (https://printables.com/@ellafoxo)

## Model files

## License

This work is licensed under a GNU (https://www.gnu.org/licenses/gpl-3.0.html)

btt_pi_tft50_v21_cover.3mf

btt_pi_tft50_v21_back_plate.3mf

btt_pi_tft50_v21_support_left_part1.3mf

btt_pi_tft50_v21_support_left_part2.3mf

btt_pi_tft50_v21_support_right.3mf

btt_pi_tft50_v21_buttons.3mf

front_grill_left.3mf

General Public License v3.0 (https://www.gnu.org/licenses/gpl-3.0.html)

✖ | Sharing without ATTRIBUTION
✔ | Remix Culture allowed
✔ | Commercial Use
✔ | Meets Open Definition
ℹ | Share under the same license

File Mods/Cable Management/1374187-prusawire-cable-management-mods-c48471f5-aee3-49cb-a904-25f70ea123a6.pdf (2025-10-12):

3D MODEL ONLY

## Summary

I'm allergic to zip-ties xD

3D Printers (https://printables.com/model?categoryId=1) > Prusa Parts & Upgrades (https://printables.com/model?categoryId=134)

Tags: | cablemanagement | prusawire

Collection of cable management mods for Prusawire. I will add more models for cable management as my Prusawire build progresses.

FAQ

PSU and Z-motor cable guide:

PSU wire spacing is designed with black Prusa PSU in mind. Holes are 3,6 mm in diameter with center to center distance of 10 mm. Hole for Z-motor cable is 4,4 mm in diameter.

Required hardware

2 x M3 T-nut for 3030 extrusion, printable version (https://www.printables.com/model/720045-printable-m3-t-nut-for-3030-extrusion-prusa-xl) if metal T-nuts are hard to find
2x M3x10 SHCS

telefaksi (https://printables.com/@telefaksi_1298577)

## Prusawire Cable Management Mods

VIEW IN BROWSER (https://printables.com/model/1374187-prusawire-cable-management-mods)

updated 5. 8. 2025 | published 5. 8. 2025

•

•

## Model files

X and Z-motor cable clips:

Designed to hold X and Z-motor cables in the little frame cutouts. Be careful when inserting heat set inserts as there is quite a thin wall around the hole. I recommend using heat set insert press.

Required hardware:

3 x M3x16 SHCS
3 x M3 Threaded Insert - M3x5x4 (Voron spec)

## This remix is based on

Prusawire 2025.B1 (BETA 1) (https://printables.com/model/1363547-prusawire-2025b1-beta-1) by Ella Fox (https://printables.com/@ellafoxo)

•
•

STEP source files; 2 files; Fusion source files; prusawire_psu_and_z-motor_cable_guide.step; prusawire_x_and_z-motor_cable_clips.step; prusawire_psu_and_z-motor_cable_guide.f3d

- Updated with counterbore bridging

## License

This work is licensed under a GNU

General Public License v3.0 (https://www.gnu.org/licenses/gpl-3.0.html)

✖ | Sharing without ATTRIBUTION prusawire_x_and_z-motor_cable_clips.f3d

prusawire_psu_and_z-motor_cable_guide_top.3mf

prusawire_psu_and_z-motor_cable_guide_bottom.3mf

prusawire_x-motor_cable_clip_front.3mf

prusawire_x-motor_cable_clip_rear.3mf

prusawire_z-motor_cable_clip_front.3mf

prusawire_z-motor_cable_clip_rear.3mf

✔ | Remix Culture allowed
✔ | Commercial Use
✔ | Meets Open Definition
ℹ | Share under the same license

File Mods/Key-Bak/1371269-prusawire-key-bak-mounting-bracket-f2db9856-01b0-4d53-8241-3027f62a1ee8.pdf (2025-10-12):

## Prusawire Key-bak mounting bracket

Summary; Tags:; keybak; prusawire; Required hardware:; telefaksi; updated 4. 8. 2025 | published 4. 8. 2025; 3D MODEL ONLY

VIEW IN BROWSER (https://printables.com/model/1371269-prusawire-key-bak-mounting-bracket)

Prusawire Key-bak mounting bracket

3D Printers (https://printables.com/model?categoryId=1) > Prusa Parts & Upgrades (https://printables.com/model?categoryId=134)

Mounting bracket for Key-bak.

3 pcs M3x12 SHCS
1 pc M3x20 or M3x16 SHCS, both work
4 pcs M3 Threaded Insert - M3x5x4 (Voron spec)
1 pc Key-bak Super48 36" 13oz (Voron Switchwire spec)

Anchor mounting to the gantry is the same as in door puller version. Same
goes for mounting the bracket to the frame, same hardware as in door
puller version. Counterweight idler doesn't require any modifications so
print parts needed for that from Prusawire files.

This remix is based on

## Model files

Prusawire 2025.B1 (BETA 1) (https://printables.com/model/1363547-prusawire-2025b1-beta-1) by Ella Fox (https://printables.com/@ellafoxo)

STEP source files; 2 files; Updated with counterbore bridging; Fusion source files; prusawire_key-bak_bracket.step; prusawire_key-bak_anchor.step; prusawire_key-bak_bracket.f3d; prusawire_key-bak_anchor.f3d

- Updated with counterbore bridging

key-bak_anchor.3mf

key-bak_anchor_cap.3mf

- Updated with counterbore bridging

## License

This work is licensed under a GNU

General Public License v3.0 (https://www.gnu.org/licenses/gpl-3.0.html)

✖ | Sharing without ATTRIBUTION
✔ | Remix Culture allowed
✔ | Commercial Use
✔ | Meets Open Definition
ℹ | Share under the same license

key-bak_bracket_plate.3mf

key-bak_bracket_left.3mf

key-bak_bracket_right.3mf

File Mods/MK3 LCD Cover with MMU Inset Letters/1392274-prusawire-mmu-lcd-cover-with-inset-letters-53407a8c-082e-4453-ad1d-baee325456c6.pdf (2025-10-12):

3D MODEL ONLY

## Summary

Instead of the letters/symbol being flush with the rest of the face plate, I made it inset with colors at the back.

3D Printers (https://printables.com/model?categoryId=1) > Other Printer Parts & Upgrades (https://printables.com/model?categoryId=2)

Tags: | mmu3 | prusawire

This is a modified MMU version of the LCD cover for the Prusawire 2025.B1 (https://www.printables.com/model/1363547-prusawire-2025b1-beta-1) by Ella Fox. (https://www.printables.com/@ellafoxo) Instead of the letters being flush, there are modifier boxes (and cylinder) behind the letters that allow you to have the colors inset. It works better than just painting on the surface, since this technique forces the slicer to bridge across the letters.

The MMU file was prepared in PrusaSlicer 2.9.2.

Bambu Studio version of the 3mf was kindly provided by erikbuild (https://www.printables.com/@erikbuild)

## This remix is based on

einarjh (https://printables.com/@einarjh_110431)

## Prusawire MMU LCD Cover with inset letters

VIEW IN BROWSER (https://printables.com/model/1392274-prusawire-mmu-lcd-cover-with-inset-letters)

updated 23. 8. 2025 | published 23. 8. 2025

## Model files

Prusawire 2025.B1 (BETA 1) (https://printables.com/model/1363547-prusawire-2025b1-beta-1) by Ella Fox (https://printables.com/@ellafoxo)

- File compatible with PrusaSlicer/Prusa MMU3
- File compatible with Bambu Studio/AMS

## License

This work is licensed under a GNU

General Public License v3.0 (https://www.gnu.org/licenses/gpl-3.0.html)

✖ | Sharing without ATTRIBUTION
✔ | Remix Culture allowed
✔ | Commercial Use
✔ | Meets Open Definition
ℹ | Share under the same license

mmu_lcd_cover_mk3_mmu.3mf

mmu_lcd_cover_mk3_bambu-ams.3mf

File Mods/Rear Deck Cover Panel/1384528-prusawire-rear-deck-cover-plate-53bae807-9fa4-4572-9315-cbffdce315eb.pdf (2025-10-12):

3D MODEL ONLY

## Summary

Rear deck cover plate for the Prusawire 3D Printer to cover exposed wiring. Supports multiple power supplies.

3D Printers (https://printables.com/model?categoryId=1) > Prusa Parts & Upgrades (https://printables.com/model?categoryId=134)

Tags: | 3dprinter | voron | switchwire | prusawire

A rear deck cover panel to cover exposed wiring (particularly for those using the WAGO holder block) on the Prusawire 3D Printer.

NOTE this is currently designed against the Beta 1 Y-Axis parts. These are changing in the future which may require a revision to the rear deck cover panels!
Parts

Left Side Piece:

deck_panel_rear_connector_m3_erikbuild-v20250814.stl

Has three holes for M3x10 FHCS

Connector Block:

deck_panel_rear_connector_m3_erikbuild-v20250814 erikbuild (https://printables.com/@erikbuild)

## Prusawire Rear Deck Cover Plate

VIEW IN BROWSER (https://printables.com/model/1384528-prusawire-rear-deck-cover-plate)

updated 15. 8. 2025 | published 15. 8. 2025

Designed to accept 4x Voron Spec M3 Heat Inserts - M3x5x4

Right Side Piece - Prusa Black (Delta) PSU:

deck_panel_rear_m3_countersunk_left_deltablackpsu_erikbuild-v20250814

Requires 3x M3 - 3030 T-Nuts (see below).

Requires 6x M3x10 FHCS (see below).

Right Side Piece - Prusa Silver (Old) PSU / Meanwell LRS-350-24 / Meanwell RSP-320-24 PSU:

deck_panel_rear_m3_countersunk_right_silverpsu-meanwellpsu_erikbuild-v20250814

Requires 2x M3 - 3030 T-Nuts (see below).

Requires 5x M3x10 FHCS (see below).

This variant features a little power cable pass-through port since these power supplies route the 24V power lines out the back. The pass-through features little slots for zip ties to secure the wiring and avoids typical placement of the WAGO connector terminal block holder.
Hardware Required

9-10x M3x10 FHCS
depending on how many screws needed for the right side piece 4x Heat Inserts M3x5x4 (Voron Spec)
5-6x M3 roll-in T-Nut for 3030 Extrusion
Prusa sells this as M3nEs
I used this EXCELLENT model (https://www.printables.com/model/720045-printable-m3-t-nut-for-3030-extrusion-prusa-xl) to print the nut and added the M3x5x4 heat inserts to them.
Print Specs

Voron Print Specs
Layer height: 0.2mm
Extrusion width: 0.4mm, forced Infill percentage: 40%
Infill type: gyroid
Wall count: 4
Solid top/bottom layers: 5 Supports: NONE
I chose Prusament Galaxy Black ASA.

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
## Model files

Change Log

v20250814-5: Improved M3 screw hole diameter and chamfer to Voron Design specs for easy installation.

v20250814-3: Fixed through-hole on the connector piece to allow M3x10 and longer screws.

v20250814-1: Initial release.

## This remix is based on

Prusawire 2025.B1 (BETA 1) (https://printables.com/model/1363547-prusawire-2025b1-beta-1) by Ella Fox (https://printables.com/@ellafoxo)

- Prusa Black PSU
- Prusa Silver PSU / Meanwell LRS-350-24 PSU / Meanwell RSP-320-24 PSU
- Prusa Black PSU

deck_panel_rear_m3_countersunk_left_deltablackpsu_e… .stl

deck_panel_rear_connector_m3_erikbuild-v20250814-5.stl

deck_panel_rear_m3_countersunk_right_silverpsu-mean… .stl

deck_panel_rear_m3_countersunk_right_deltablackpsu_… .stl

deck_panel_rear_m3_countersunk_erikbuild-v20250814-5 .f3d

## License

This work is licensed under a GNU

General Public License v3.0 (https://www.gnu.org/licenses/gpl-3.0.html)

✖ | Sharing without ATTRIBUTION
✔ | Remix Culture allowed
✔ | Commercial Use
✔ | Meets Open Definition
ℹ | Share under the same license

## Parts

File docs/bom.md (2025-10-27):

---
layout: default
title: "Bill of Materials"
nav_order: 4
---

# Bill of Materials (BOM)

The latest BOM can be [found on GitHub in the BOM folder](https://github.com/Positron3D/Prusawire/tree/main/BOM).

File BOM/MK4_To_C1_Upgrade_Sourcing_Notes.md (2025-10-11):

# Notes from the Mk4/4S to Core One Upgrade Path

When starting with the remnants of the Mk4/4s to Core One Upgrade Kit From Prusa Reserch, you will have the following itemes:

- 8mmx370 X-axis smooth rods
- LM8UU and LM10LUU bearings
- Rubber feet
- Frame and front/rear plates, base extrusions etc.
- Y carriage
- Bearing clips
- Spacer 3.2x6x8mm (Prusa included a spare in the MK4s kit)
- Print sheets
- Spool holder
- The cable wraps and nylon stiffeners inside them
- Heatbed power cables

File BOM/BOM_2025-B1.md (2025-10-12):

# Prusawire 2025.B1 Bill of Materials

This Bill of Materials is accurate for Prusawire version 2025.B1

## Hardware Kit Sources
[KB-3D: BOM Hardware / Fastener Kit - Prusawire - Beta 1](https://kb-3d.com/store/configurators/5743-bom-hardware-fastener-kit-prusawire-beta-1-1755965660392.html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) (affiliate link)

[West3D: Prusawire Stainless Steel Fastener Kit (BDF)](https://collabs.shop/d4usq3) (affiliate link)

| Category | Component | Standard | Optional? | Qty | Notes | Alternative Source 1 | Alternative Source 2 | Alternative Source 3 | Alternative Source 4 |
| --- | --- | --- | --- | --- | --- | --- | --- | --- | --- |
| **Filament** | Primary Color (Black) | PC, ASA, ABS | | 1 | Recommended a carbon or glass filled material to prevent warpage on larger parts. If you cannot print this, then bed adhesive and patience with PC, ABS, or ASA are advised. | [Prusament PC Blend CF (Prusa)](https://www.prusa3d.com/product/prusament-pc-blend-carbon-fiber-black-800g-6)<br>[Affiliate Link](https://www.prusa3d.com/product/prusament-pc-blend-carbon-fiber-black-800g-6/#a_aid=nomad&a_bid=e2885a92) | [FormFutura Kratos PC CF10](https://formfutura.com/product/kratos-pc-cf/)<br><br>[USA (Fabreeko) ASA](https://www.fabreeko.com/products/3do-black-asa-fillament) | [LDO ASA-CF (EU)](https://levendigs.com/collections/filament/products/ldo-asa-cf-filament-1-75mm-1kg-black) | [3DO ASA (EU)](https://3do.dk/en/asa/502-3do-asa-1kg-black.html) |
| | Secondary Color (Red) | | | 1 | | [Prusament ASA (Prusa)](https://www.prusa3d.com/product/prusament-asa-lipstick-red-850g/)<br>[Affiliate Link](https://www.prusa3d.com/product/prusament-asa-lipstick-red-850g/#a_aid=nomad&a_bid=e2885a92) | [Polymaker PolyLite ABS](https://us.polymaker.com/products/polylite-abs?variant=39574342664249) | [LDO ASA (EU)](https://levendigs.com/products/ldo-abs-filament-1-75mm-1kg-red) | [3DO ASA (EU)](https://3do.dk/en/asa/501-814-3do-asa-1kg-red.html#/32-colour-red) |
| **Printed Parts** | Printed Parts | | | 1 | | Print it yourself | Ask a friend | Ask the Positron Discord | |
| **Fasteners** | M5x30 BHCS | ISO 7380 | | 2 | Buy extra fasteners, always! | | | | |
| | M5x16 BHCS | ISO 7380 | | 32  | | | | | |
| | M5x10 BHCS | ISO 7380 | | 4 | | | | | |
| | M5x8 BHCS | ISO 7380 | | 2 | | | | | |
| | M5 Hex Nut | DIN 934 | | 2 | | | | | |
| | M5 T-Nut for 2020 Extrusion | | | 6 | | | | | |
| | M4x10 BHCS | ISO 7380 | | 2 | | | | | |
| | M3x40 SHCS | ISO 4762 / DIN 912 | | 7 | | | | | |
| | M3x30 SHCS | ISO 4762 / DIN 912 | | 22  | Bolt Depot | KB-3D or West3D | Bolt Depot | 3DKatten or TME (EU) | |
| | M3x25 SHCS | ISO 4762 / DIN 912 | | 10  | | | | | |
| | M3x20 SHCS | ISO 4762 / DIN 912 | | 14  | | | | | |
| | M3x16 SHCS | ISO 4762 / DIN 912 | | 6 | | | | | |
| | M3x14 SHCS | ISO 4762 / DIN 912 | | 5 | | | | | |
| | M3x12 SHCS | ISO 4762 / DIN 912 | | 11  | | | | | |
| | M3x10 SHCS | ISO 4762 / DIN 912 | | 81  | | | | | |
| | M3x8 SHCS | ISO 4762 / DIN 912 | | 15  | | | | | |
| | M3x10 BHCS | ISO 7380 | | 11  | Low profile bed cable mount | | | | |
| | M3x30 BHCS | ISO 7380 | | 1 | Used for the Y idler bearing stack. **FYI: 2025.B1 Printables Release from @EllaFoxo and matching hardware kits from KB-3D and West3D may not yet include this!** | | | | |
| | M3x8 BHCS | ISO 7380 | | 3 | | | | | |
| | M3x6 BHCS | ISO 7380 | Yes | 9 | Used for the newer bed expansion joints. Optional if you use the classic MK3 spacers. | | | | |
| | M3x4 FHCS | ISO 10642 | Yes | 8 | | | | | |
| | M3x16 FHCS | ISO 10642 | Yes | 1 | Used for the MK52 bed in the center. Optional if you use the classic MK3 spacers. | | | | |
| | M3 Shim Washer 3x6x0.5mm | DIN 988 | | 35  | Absolutely do not use normal washers. These must be shim washers built to higher tolerances. | [KB-3D](https://kb-3d.com/store/inserts-fasteners-adhesives/287-3x6x05mm-shim-ring-washer-pack-of-50-din988-1634423217623.html)<br>[Affiliate Link](https://kb-3d.com/store/inserts-fasteners-adhesives/287-3x6x05mm-shim-ring-washer-pack-of-50-din988-1634423217623.html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) | [Replimat Labs (EU)](https://www.replimat.eu/3x6x0.5mm-shim-ring-din-988-40-pcs/rt10079) | [TME (EU)](https://www.tme.eu/de/en/details/b3_6_0.5_bn1976/washers/bossard/1225340/) | [TME (USA)](https://www.tme.com/us/en-us/details/b3_6_0.5_bn1976/washers/bossard/1225340/) |
| | M3 Nylon Lock Nut | DIN 985 | Yes | 7 | 1x needed for y_idler_block. The rest are for Older MK3 Y carriage (if you have the newer MK4 Y carriage, 6x can be eliminated.) | | | | |
| | M3 Hex Nut | DIN 934 | | 10  | 1x needed for y_idler_block. | | | | |
| | M3 Square Nut | DIN 562 | | 14  | Prusa-style M3 Square Nut (Slim) is ideal, but V0 Square Nuts now work! | | | | |
| | M3 Threaded Insert - M3x5x4 (Voron spec) | | | 100 | Buy extra! | [CNC Kitchen (EU)](https://cnckitchen.store/products/made-for-voron-gewindeeinsatz-threaded-insert-m3x5x4-100-stk-pcs) | [Vector3D (UK)](https://vector3d.shop/products/heat-set-insert-m3-voron) | | |
| | M3 T-Nut for 3030 Extrusion | | Yes | 28  | This can be really annoying to source, so we included a printable version instead which uses a heat set insert. Getting the metal ones is totally optional. | [Prusa](https://www.prusa3d.com/product/psu-holder-m3ne-2/)<br>[Affiliate Link](https://www.prusa3d.com/product/psu-holder-m3ne-2/#a_aid=nomad&a_bid=e2885a92) | [KB-3D](https://kb-3d.com/store/extrusion-framing/245-t-nut-roll-in-30-series-8mm-slot-width-m3-threads-1657989315930.html)<br>[[Affiliate Link]](https://kb-3d.com/store/extrusion-framing/245-t-nut-roll-in-30-series-8mm-slot-width-m3-threads-1657989315930.html) | | |
| | M3 T-Nut for 2020 Extrusion | | | 10  | | | | | |
| | M2x10 Self-Tapping Screw for Plastics | | | 4 | Raspberry Pi mounting | | | | |
| **Motion** | GATES GT2 Open Belt LL-2GT-6 (6mm wide) - 1600mm | | | 2 | Genuine GATES belts are required for every open loop belt on the machine. Don't bother with the clones. | [KB-3D](https://kb-3d.com/store/motion/215-gates-powergrip-2gt-belt-open-6mm-width.html)<br>[Affiliate Link](https://kb-3d.com/store/motion/215-gates-powergrip-2gt-belt-open-6mm-width.html?affp=22155) | [West3D](https://west3d.com/products/gates-gt2-open-belt-ll-2gt-6-6mm-wide-voron-v0-v1-v2-switchwire)<br>[Affiliate Link](https://west3d.com/products/gates-gt2-open-belt-ll-2gt-6-6mm-wide-voron-v0-v1-v2-switchwire?dt_id=524416) | [3DKatten (EU)](https://3dkatten.se/products/gates-power-grip-gt-ll-2gt-epdm-balte-1-meter?variant=48182522741059) | |
| | GATES GT2 Open Belt LL-2GT-6 (6mm wide) - 1000mm | | | 1 | [Levendigs (EU)](https://levendigs.com/products/gates-2gt-belt-1cm) | | | | |
| | GT2 20T (6mm wide) Pulley (5mm bore) | | | 3 | | [KB-3D](https://kb-3d.com/store/motion/213-gates-powergrip-2gt-pulley-20-tooth-5mm-6mm-1634481851944.html)<br>[Affiliate Link](https://kb-3d.com/store/motion/213-gates-powergrip-2gt-pulley-20-tooth-5mm-6mm-1634481851944.html?affp=22155) | [West3D](https://west3d.com/products/black-pulleys-and-idlers-gt2-20t-gt2-16t?variant=42151451525332)<br>[Affiliate Link](https://west3d.com/products/black-pulleys-and-idlers-gt2-20t-gt2-16t?variant=42151451525332&dt_id=524416) | [3DKatten (EU)](https://3dkatten.se/products/20t-2gt-5mm-id-pulley?variant=48182169600323) | |
| | F623-2RS Bearing | | | 20  | Don't cheap out here. Use quality bearings for smooth printer operation and longevity. | [KB-3D](https://kb-3d.com/store/magnets-bearings/168-3x10x4-flanged-metric-ball-bearing-f623-2rs-6440891415288.html)<br>[Affiliate Link](https://kb-3d.com/store/magnets-bearings/168-3x10x4-flanged-metric-ball-bearing-f623-2rs-6440891415288.html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) | [West3D](https://west3d.com/products/f623-2rs-flange-ball-bearing)<br>[Affiliate Link](https://west3d.com/products/f623-2rs-flange-ball-bearing?dt_id=524416) | [Replimat (EU [DE])](https://www.replimat.eu/fushi-f623-2rs-abec-7/rt10209) | [AliExpress (Rain & Dew)](https://www.aliexpress.com/item/1005008564381498.html) |
| | Linear Rail MGN12H (300mm), Z1 preload | | | 1 | Z1 preload recommended | [KB-3D](https://kb-3d.com/store/motion/377-5160-kb3d-mgn12h-linear-rail-guide-with-carriage-multiple-lengths-1646161437836.html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)<br>[Affiliate Link](https://kb-3d.com/store/motion/377-5160-kb3d-mgn12h-linear-rail-guide-with-carriage-multiple-lengths-1646161437836.html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) | [West3D](https://west3d.com/products/west3d-printing-mgn12h-1r-300-350-400-linear-rails-with-carriages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)<br>[Affiliate Link](https://west3d.com/products/west3d-printing-mgn12h-1r-300-350-400-linear-rails-with-carriages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) | [3DO (EU)](https://3do.dk/en/linear-rails/1169-1567-ldo-stainless-mgn12h-rail-z1-preload.html#/96-length-300mm) | [Hobby-Store.pl (EU, request length)](https://hobby-store.pl/en/linear-rails/mgn12-linear-rail-400mm-with-mgn12h-carriage.html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) |
| | 8x370mm Linear Rod | | | 2 | X Axis rods, reused for the Y axis | [Prusa](https://www.prusa3d.com/product/smooth-rod-x-axis-mk4-mk3-s-mk2-5-s-mk2-s/)<br>[Affiliate Link](https://www.prusa3d.com/product/smooth-rod-x-axis-mk4-mk3-s-mk2-5-s-mk2-s/#a_aid=nomad&a_bid=e2885a92) | | | |
| | 8x320 or 10x325 Linear Rod | | | 2 | Z Axis rods from MK3/4 | | | | |
| | LM8UU Bearing | | | 3 | | [Prusa](https://www.prusa3d.com/product/linear-bearing-lm8uu/)<br>[Affiliate Link](https://www.prusa3d.com/product/linear-bearing-lm8uu/#a_aid=nomad&a_bid=e2885a92) | [West3D](https://west3d.com/products/lm8uu-smooth-rod-8x15x45-linear-bearing)<br>[Affiliate Link](https://west3d.com/products/lm8uu-smooth-rod-8x15x45-linear-bearing?dt_id=524416) | [Levendigs (EU)](https://levendigs.com/products/myt-lm8uu-linear-bearing-1pc) | [3DO (EU)](https://3do.dk/en/bearings/385-lm8uu.html) |
| | LM10LUU Bearing | | | 2 | These are the Z bearings on MK4. If you are using 8mm rods on Z, replace each 1x LM10LUU with 2x LM8UU instead. | [Prusa](https://www.prusa3d.com/product/linear-bearing-lm10luu/)<br>[Affiliate Link](https://www.prusa3d.com/product/linear-bearing-lm10luu/#a_aid=nomad&a_bid=e2885a92) | | [Levendigs (EU)](https://levendigs.com/products/myt-lm10luu-linear-bearing-1pc) | |
| | Automatic Door Puller, 1kg pull force | | | 1 | This is used in place of a branded Key-Bak, as it is more accessible to purchase outside of the USA.  Remixes for Switchwire spec (*Key-Bak Super48 36in 13oz*) exist as well. | [Amazon (USA)](https://www.amazon.com/dp/B0F2M9GKDT) | [Amazon (Germany)](https://www.amazon.de/dp/B0BRVBHQ1J) | | |
| **Motors (pick one)** | Prusa MK3 X/Y/Z/E Motor | | | 3 | When upgrading directly from MK3 or MK4, the motors used are as follows:  <br>X motor: X axis (left side)  <br>Y motor: Y axis  <br>E motor: Z axis (right side) | Not recommended for new builds, only converting to Prusawire from old hardware | | | |
| | Prusa MK4 X/Y/Z/E Motor | | | | | | | | |
| | LDO 42STH40-1684AC | | | 3 | These steppers are frequently found in Switchwire motor kits. They also sometimes come with the motor required for Stealthburner.  <br>  <br>Use this option when you are building from the leftovers of your Core ONE upgrade kit.<br><br>If using Stealthburner/CW2, consider Switchwire Stepper Kit (with the pancake motor) | [KB-3D](https://kb-3d.com/store/electronics/436-ldo-voron-switchwire-stepper-motor-kit-4-piece-rev-c-1640807333865.html)<br>[Affiliate Link](https://kb-3d.com/store/electronics/436-ldo-voron-switchwire-stepper-motor-kit-4-piece-rev-c-1640807333865.html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) | [onetwo3d (UK)](https://www.onetwo3d.co.uk/product/voron-switchwire-stepper-motor-kit-by-ldo/) | [Blurolls (ships from China)](https://www.blurolls3d.com/products/blurolls-voron-switchwire-3d-printer-motors-kit-made-by-ldo-stepper-motor-kit-3pcs-ldo-42sth40-1684ac-1pc-ldo-36sth20-1004ahg)  | |
| Vibration Management | Rubber Machine Foot 14x11x9mm | | | 4 | | [Replimat Labs (EU)](https://www.replimat.eu/4x-rubber-feet-14x11x9mm-for-v0.2-black/rt10118) | [KB-3D](https://kb-3d.com/store/frame-enclosure/283-rubber-machine-foot-14x11x9mm-set-of-4.html)<br>[Affiliate Link](https://kb-3d.com/store/frame-enclosure/283-rubber-machine-foot-14x11x9mm-set-of-4.html?affp=22155) | [West3D](https://west3d.com/products/14x11x9mm-little-rubber-feet-with-steel-washer)<br>[Affiliate Link](https://west3d.com/products/14x11x9mm-little-rubber-feet-with-steel-washer?dt_id=524416) | |
| **Power Supply (pick one)** | Delta PMZ-24V240WDAL | Prusa Black PSU | | 1 | **The Prusa black PSU is recommended for new builds.**  <br>If you are upcycling an old Prusa with the silver PSU, you can continue to use it. | [Prusa](https://www.prusa3d.com/product/psu-24v-240w-assembly/)<br>[Affiliate Link](https://www.prusa3d.com/product/psu-24v-240w-assembly/#a_aid=nomad&a_bid=e2885a92) | [Printed Solid](https://www.printedsolid.com/products/original-prusa-psu-24v-240w-assembly) | | |
| | PRPZ-24-240 | Prusa Silver PSU | | 1 | Second hand only; only if you have one lying around. | | | | |
| | Meanwell LRS-350-24 | Meanwell PSU | | | Great for USA users, do not use in EU (use RSP-320-24 instead). | [KB-3D](https://kb-3d.com/store/power-supplies-converters/185-meanwell-lrs-350-24-power-supply-24v-350w.html)<br>[Affiliate Link](https://kb-3d.com/store/power-supplies-converters/185-meanwell-lrs-350-24-power-supply-24v-350w.html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) | [West3D](https://west3d.com/products/mean-well-lrs-350-24-150w-24v-6-5a-power-supply-psu)<br>[Affiliate Link](https://west3d.com/products/mean-well-lrs-350-24-150w-24v-6-5a-power-supply-psu?dt_id=524416)<br> | [Digikey](https://www.digikey.com/en/products/detail/mean-well-usa-inc/LRS-350-24/7705034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) | |
| **Mainboard (pick one)** | Einsy RAMBo | | | 1 | | [Prusa](https://www.prusa3d.com/product/einsy-rambo-mk3-s/)<br>[Affiliate Link](https://www.prusa3d.com/product/einsy-rambo-mk3-s/#a_aid=nomad&a_bid=e2885a92) | [Printed Solid](https://www.printedsolid.com/products/original-prusa-einsy-rambo-mk3s) | | |
| | BigTreeTech SKR Mini E3 v3.0 | | | 1 | | [KB-3D](https://kb-3d.com/store/controllers-displays-drivers/420-bigtreetech-skr-mini-e3-v30-32-bit-control-board-1639888431041.html)<br>[Affiliate Link](https://kb-3d.com/store/controllers-displays-drivers/420-bigtreetech-skr-mini-e3-v30-32-bit-control-board-1639888431041.html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) | [West3D](https://west3d.com/products/btt-skr-mini-e3-v3-controller-board-3d-printer-control-system)<br>[Affiliate Link](https://west3d.com/products/btt-skr-mini-e3-v3-controller-board-3d-printer-control-system?dt_id=524416) | | |
| **Frame** | Printer Frame | | | 1 | MK3/S/+ has an older version of this frame. The MK4 version is perforated with hexagons at the rear to reduce weight, and is also a little thicker.  <br>Both versions are absolutely fine for this build. | [Prusa](https://www.prusa3d.com/product/printer-frame/)<br>[Affiliate Link](https://www.prusa3d.com/product/printer-frame/#a_aid=nomad&a_bid=e2885a92) | | | |
| | Front Plate | | | 1 | Stock Prusa MK3 or MK4 | [Prusa](https://www.prusa3d.com/product/front-plate/)<br>[Affiliate Link](https://www.prusa3d.com/product/front-plate/#a_aid=nomad&a_bid=e2885a92) | | | |
| | Rear Plate | | | 1 | | [Prusa](https://www.prusa3d.com/product/rear-plate/)<br>[Affiliate Link](https://www.prusa3d.com/product/rear-plate/#a_aid=nomad&a_bid=e2885a92) | | | |
| | Aluminum Extrusion - Long | | | 2 | | [Prusa](https://www.prusa3d.com/product/aluminum-extrusion-long/)<br>[Affiliate Link](https://www.prusa3d.com/product/aluminum-extrusion-long/#a_aid=nomad&a_bid=e2885a92) | | | |
| | Aluminum Extrusion - Short | | | 2 | | [Prusa](https://www.prusa3d.com/product/aluminum-extrusion-short/)<br>[Affiliate Link](https://www.prusa3d.com/product/aluminum-extrusion-short/#a_aid=nomad&a_bid=e2885a92) | | | |
| | 2020 T-Slot Aluminum Extrusion - 350mm | | | 1 | This is not part of a stock Prusa frame. It will need to be purchased | [Hobby-Store.pl (EU)](https://hobby-store.pl/en/aluminium-profile-2020-type-t-slot/altrax-aluminium-profile-2020-t-slot-type-matt-black.html) | [DLLPDF (Custom length)](https://dllpdf.com/dllpdf-2020-by-the-mm) | [Misumi (USA)](https://us.misumi-ec.com/vona2/detail/110302683830/?HissuCode=HFSB5-2020-350) | [Misumi (EU)](https://de.misumi-ec.com/vona2/detail/110302683830/?HissuCode=HFSB5-2020-350) |
| **Bed Assembly** | Y Carriage | | | 1 | The newer MK4 carriage has perforated hexagonal holes on the bottom to reduce weight.  <br>Both the classic MK3 and the MK4 versions are supported. | [Prusa](https://www.prusa3d.com/product/y-carriage/)<br>[Affiliate Link](https://www.prusa3d.com/product/y-carriage/#a_aid=nomad&a_bid=e2885a92) | [West3D (TriangleLab)](https://west3d.com/products/prusa-mk3-y-carrier-trianglelab)<br>[[Affiliate Link]](https://west3d.com/products/prusa-mk3-y-carrier-trianglelab?dt_id=524416) | [OneTwo3D (LDO) (UK)](https://www.onetwo3d.co.uk/product/ldo-switchwire-y-carriage/) | |
| | Bearing Clips | | | 3 | If you do not have these currently, buy the newer MK4 ones with the rubber spacer, as it makes the bearings slide nicer.  <br>MK3 ones will work fine too. | [Prusa](https://www.prusa3d.com/product/bearing-clips/)<br>[Affiliate Link](https://www.prusa3d.com/product/bearing-clips/#a_aid=nomad&a_bid=e2885a92) | | | |
| | MK52 Heated Bed (24V) | | | 1 | | [Prusa](https://www.prusa3d.com/product/magnetic-heatbed-mk52-24v-assembly/)<br>[Affiliate Link](https://www.prusa3d.com/product/magnetic-heatbed-mk52-24v-assembly/#a_aid=nomad&a_bid=e2885a92) | [KB-3D](https://kb-3d.com/store/heated-bed-electronics/812-ldo-motors-heated-bed-for-switchwire-prusa-mk3-magnetic-24v-1677363868661.html)<br>[Affiliate Link](https://kb-3d.com/store/heated-bed-electronics/812-ldo-motors-heated-bed-for-switchwire-prusa-mk3-magnetic-24v-1677363868661.html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) | [3Dmensionals (EU)](https://www.3dmensionals.de/ldo-24v-magnetic-heatbed-948#attr=9122,13592,9125,9126,23242) | |
| | Expansion Joints (Set) | | | 8 | In place of the newer MK4 spacer and expansion joints, you could continue to use your old spacers from the MK3. | [Prusa](https://www.prusa3d.com/product/expansion-joints-set/)<br>[Affiliate Link](https://www.prusa3d.com/product/expansion-joints-set/#a_aid=nomad&a_bid=e2885a92) | | | |
| | Spacer 3.2x6x8mm | | | 1 | Prusa only sells this as part of MK4S spare parts set. | [McMaster-Carr](https://www.mcmaster.com/92871A011/) | [Prusa](https://www.prusa3d.com/product/spare-parts-mk4s-set/)<br>[Affiliate Link](https://www.prusa3d.com/product/spare-parts-mk4s-set/#a_aid=nomad&a_bid=e2885a92)<br> | [TME (EU)](https://www.tme.eu/en/details/dr336_3.2x8/metal-spacers/dremec/336-3-2x08/) | |
| | Prusa Textured PEI Sheet for MK3/4 Beds | | | 1 | | [Prusa](https://www.prusa3d.com/product/textured-powder-coated-print-sheet/)<br>[Affiliate Link](https://www.prusa3d.com/product/textured-powder-coated-print-sheet/#a_aid=nomad&a_bid=e2885a92) | | | |
| **Electronics** | Hook Up Wire - 15AWG (1.5mm) Stranded Core, Black and Red | | | 8 | | | | | |
| | Raspberry Pi 3B+, 4B+, or Zero 2W | | | 1 | Pi 5 draws a lot of power. We don't recommend it on this build. Alternative to the Pi would be an Orange Pi 4A | | | | |
| | LDO Nitehawk-SB USB Toolhead Board | | Yes | 1 | Super recommended | | | | |
| | Prusa MK3 LCD Screen | | Yes | | MK3 supported. Don't bother if you're starting from MK4 parts | | | | |
| | 5015 Blower Fan, 5V or 24V | | | 1 | Part cooling fan | | | | |
| | 4010 Axial Fan, 5V or 24V, 3 wire (tachometer) | | | 1 | Hotend cooling fan | | | | |
| | LDO Motors Input Shaper Kit | | Yes | 1 | ADXL345 and 5V wiring included for the Raspberry Pi. Super convenient | | | | |
| | 24V to 5V Step Down DC-DC Converter | | Yes | 1 | Internal powering of the Pi. | [KB-3D](https://kb-3d.com/store/power-supplies-converters/259-dc-dc-converter-1224-volt-to-5v-10-amp-50-watt-1648320892173.html) | | | |
| **(Optional) Prusa Silver PSU: Mains wiring** | IEC C14 Fused Inlet, 10A minimum | | Yes | 1 | If using Prusa Silver PSU and Frame Mount | [TME (EU)](https://www.tme.eu/en/details/pf0002_63/iec-60320-connectors/bulgin/) | [electro:kit (EU)](https://www.electrokit.com/en/natbrunn-c14-med-sakringshallare-skruv) | | |
| | ZF Electronics WRG32F2FBRLN | | Yes | 1 | If using Prusa Silver PSU and Frame Mount | [West 3D](https://west3d.com/products/zf-rocker-switch-dpst-16a-on-off-wrg32f2bbrln)<br>[Affiliate Link](https://west3d.com/products/zf-rocker-switch-dpst-16a-on-off-wrg32f2bbrln?dt_id=524416) | [Farnell (EU)](https://de.farnell.com/en-DE/zf-electronics/wrg32f2fbrln/switch-illuminated-rocker-dpst/dp/2136113) | | |
| **(Optional) Meanwell PSU: Mains Wiring** | TycoElectronics - 10EGG1-2 Filtered Power Inlet | | Yes | 1 | If using Meanwell PSU and Frame Mount | [West3D](https://west3d.com/products/tycoelectronics-10ehg1-2-filtered-power-inlet)<br>[Affiliate Link](https://west3d.com/products/tycoelectronics-10ehg1-2-filtered-power-inlet?dt_id=524416)<br> | | | |
| | ZF Electronics WRG32F2FBRLN | | Yes | 1 | If using Prusa Silver PSU and Frame Mount | [West 3D](https://west3d.com/products/zf-rocker-switch-dpst-16a-on-off-wrg32f2bbrln)<br>[Affiliate Link](https://west3d.com/products/zf-rocker-switch-dpst-16a-on-off-wrg32f2bbrln?dt_id=524416) | [Farnell (EU)](https://de.farnell.com/en-DE/zf-electronics/wrg32f2fbrln/switch-illuminated-rocker-dpst/dp/2136113) | | |
| **Cables** | HellermannTyton 170-01000 Helagaine Twist-In Cable Sleeve | 300-350mm length | | 1 | Used to wrap the MK52 bed cables. For MK3, this part is 300mm. MK3.9 and above, this is 350mm. | [Prusa](https://www.prusa3d.com/product/textile-sleeve-35-cm/) | [TME (EU)](https://www.tme.eu/de/en/details/twist-in-05-pet-bk/conduits/hellermanntyton/170-01000/) | [Conrad (EU)](https://www.conrad.com/en/p/hellermanntyton-170-01000-twist-in-05-helagaine-meshwork-hose-black-541298.html) | |
| | HellermannTyton 170-01001 5-8mm Helagaine Twist-In Cable Sleeve | 520mm length | | 1 | Prusa Nextruder cable sleeving. Used for the toolhead | [Prusa](https://www.prusa3d.com/product/textile-sleeve-8x520-mm/) | [TME (EU)](https://www.tme.eu/de/en/details/twist-in-08-pet-bk/conduits/hellermanntyton/170-01001/) | | |
| | 2mm or 3mm Nylon - 555mm | | | 1 | This is the nylon used on Nextruder. It will be used for the Stealthburner wiring.  <br>It can also be used on the heated bed if you don't have your old nylon anymore. If that is the case, by two of them. | [Prusa](https://www.prusa3d.com/product/nylon-3x555-mm/) | | | |
| **Spool Management** | ECAS Bowden Collet 4mm | | Yes | 2 | | | | | |
| | PTFE Tube 4mm OD, 3mm ID, 500mm | | Yes | 1 | Cut to length | | | | |
| | PTFE Tube 4mm OD, 2mm ID, 50mm | | | 1 | For the hotend. Capricorn is suggested if you have it. | | | | |
| | Prusa Spool Holder | | Yes | 1 | Printable version can be used instead | | | | |
| **Z Probe (pick one)** | SuperPINDA | | | 1 | Temp until load cell Z probing. If you are using the older PINDAv2 or v1, we suggest replacing it to improve Z offset stability | | | | |
| | Omron TL-Q5MC2-Z | | | | | | | | |

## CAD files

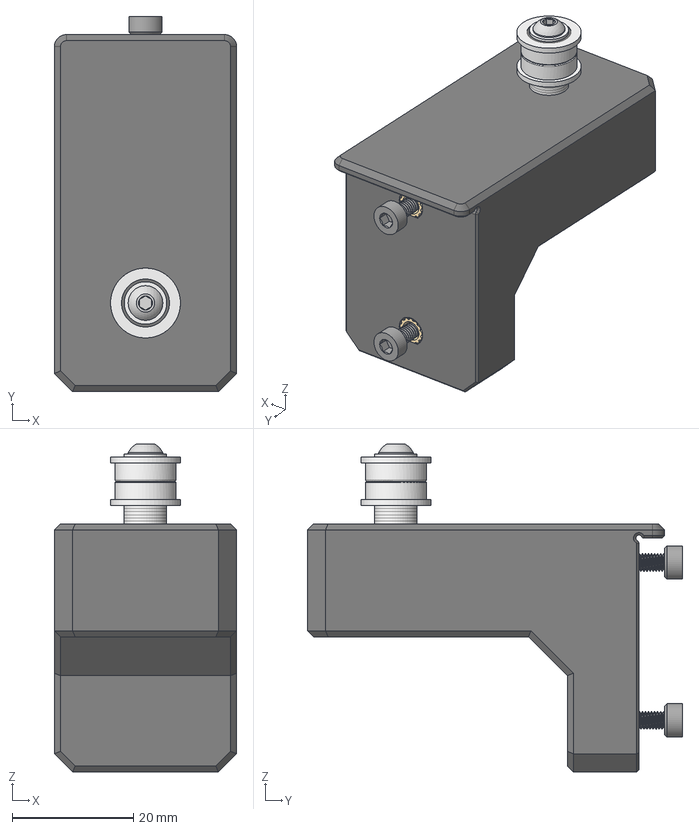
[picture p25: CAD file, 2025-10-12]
CAD/Y_Axis/Y Idler Assembly.step
30.0 x 61.8 x 54.0 mm
M3x10 SHCS x 2
y_idler_bracket v14
M3 Threaded Insert x 2
M3 Shim Washer x 7
F623 Bearing x 2
92095A187_Button Head Hex Drive Screw
91828A211_18-8 Stainless Steel Hex Nut
93625A100_18-8 Stainless Steel Nylon-Insert Locknut

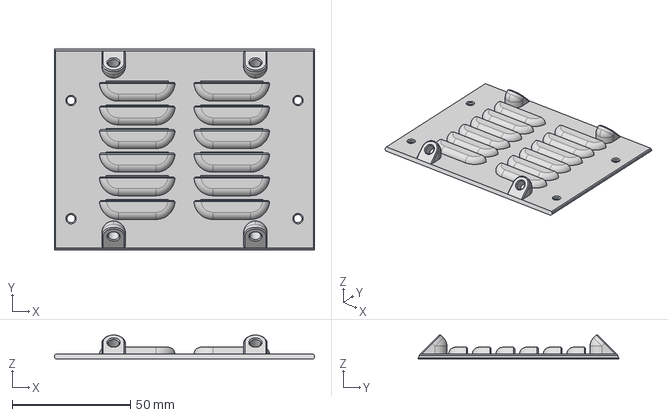
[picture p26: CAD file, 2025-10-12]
Mods/xBuddy Box Electronics Tower/STEP/lower_electronics_main_cover.step
110.0 x 85.2 x 10.1 mm

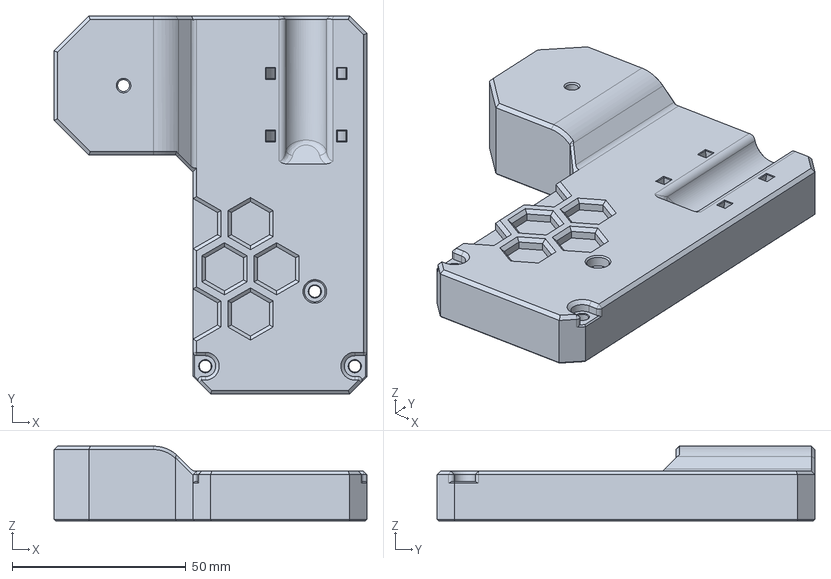
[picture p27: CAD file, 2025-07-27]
CAD/Door_Puller/door_puller_idler_bracket.step
90.0 x 108.7 x 21.5 mm

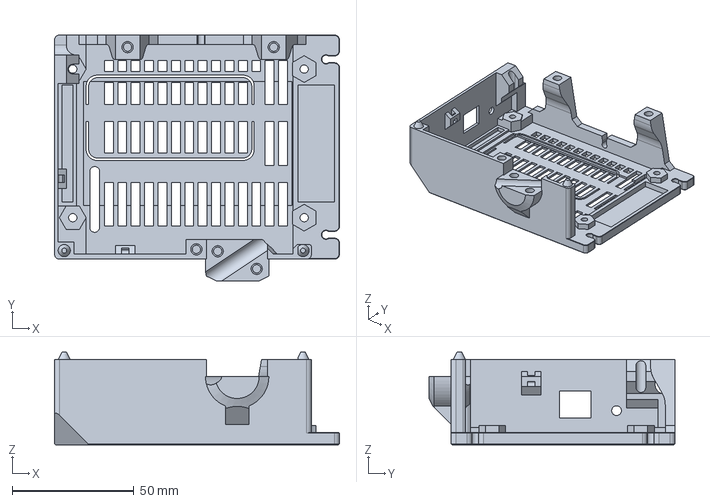
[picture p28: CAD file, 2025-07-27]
CAD/Electronics/mcu_box_einsy.step
117.0 x 101.0 x 38.0 mm

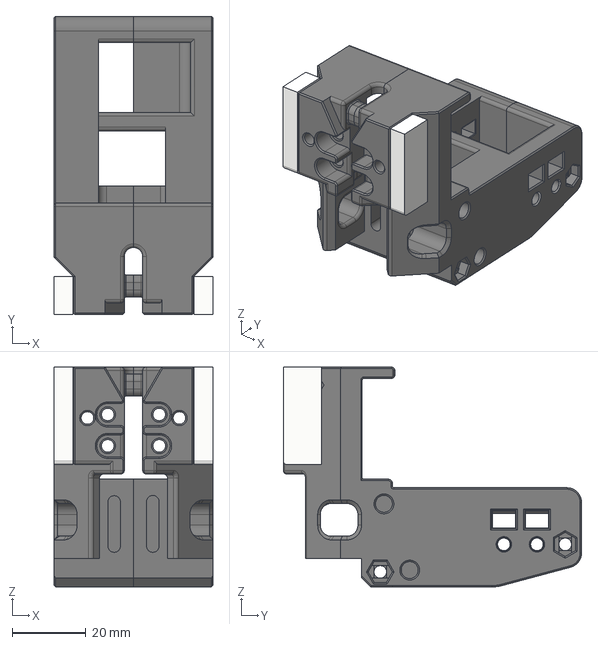
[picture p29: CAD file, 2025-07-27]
CAD/Experimental_X_Carriages/x_carriage_db_anthead.step
43.2 x 81.1 x 59.8 mm

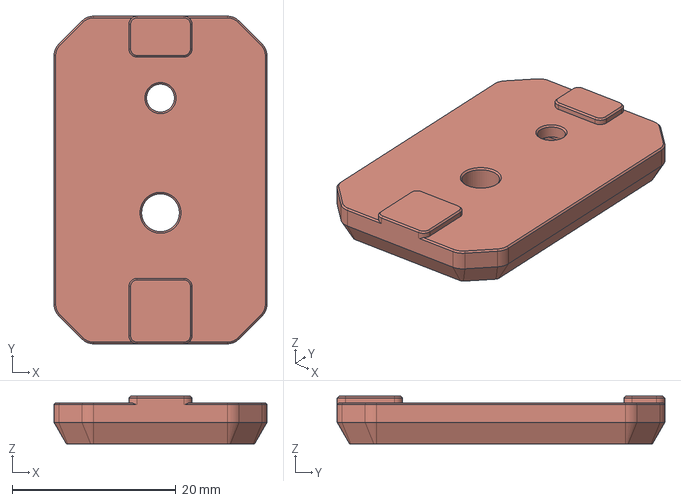
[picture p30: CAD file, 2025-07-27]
CAD/Frame/[a]_rubber_foot_block_x4.step
26.0 x 40.0 x 5.80 mm

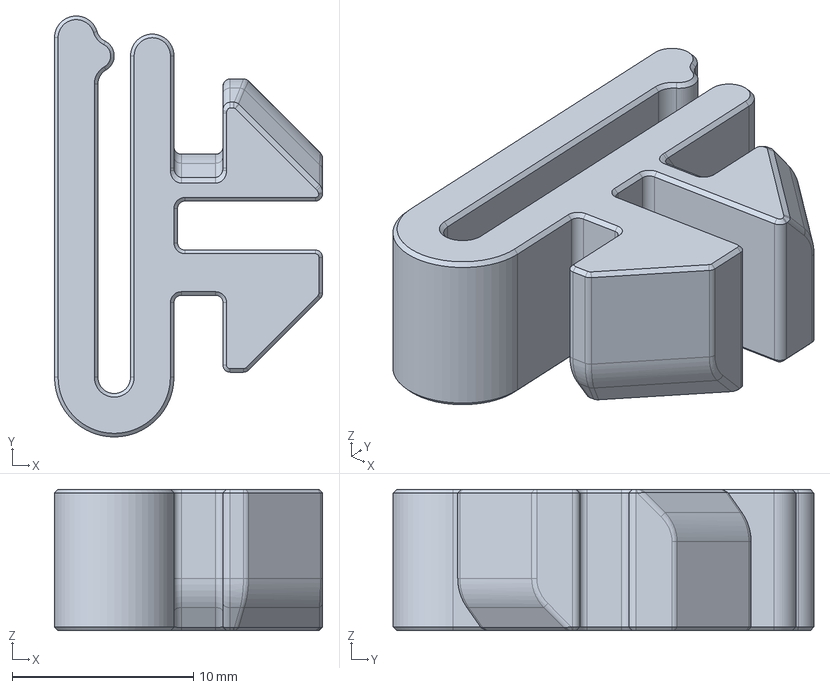
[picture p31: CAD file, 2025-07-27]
CAD/MK3_LCD/lcd_cable_clip_x4.step
14.8 x 23.2 x 7.80 mm

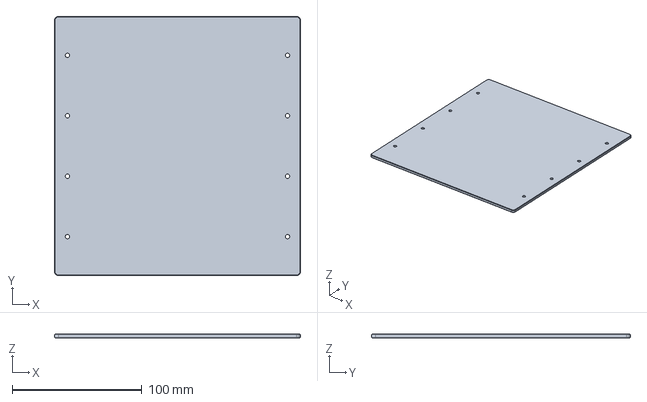
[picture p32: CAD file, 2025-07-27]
CAD/Panels/deck_panel_front.step
190.0 x 200.0 x 3.00 mm

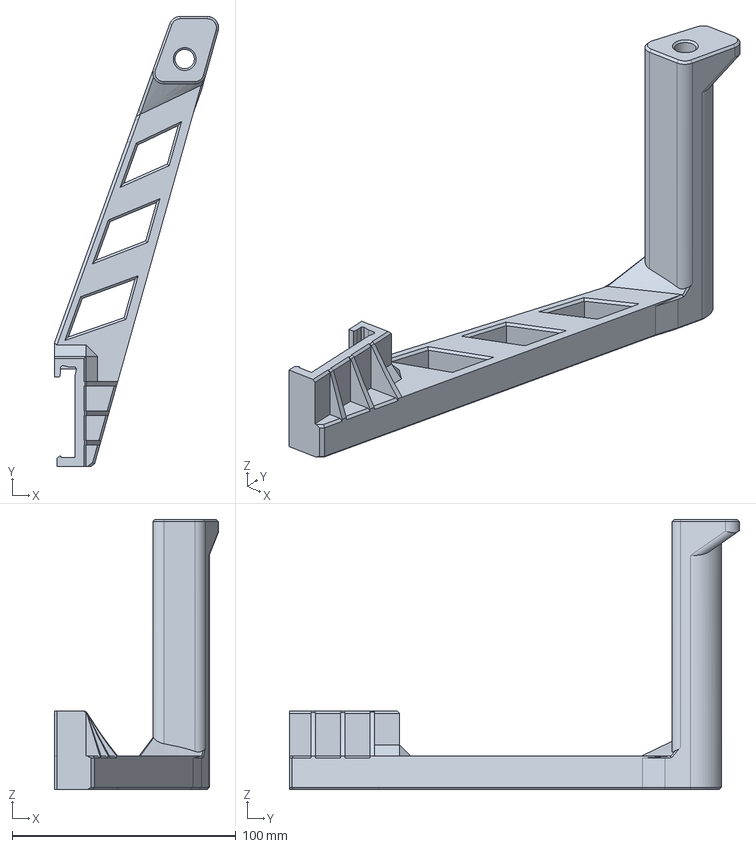
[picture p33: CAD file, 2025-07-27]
CAD/Spool_Management/spool_holder.step
73.4 x 200.9 x 120.6 mm

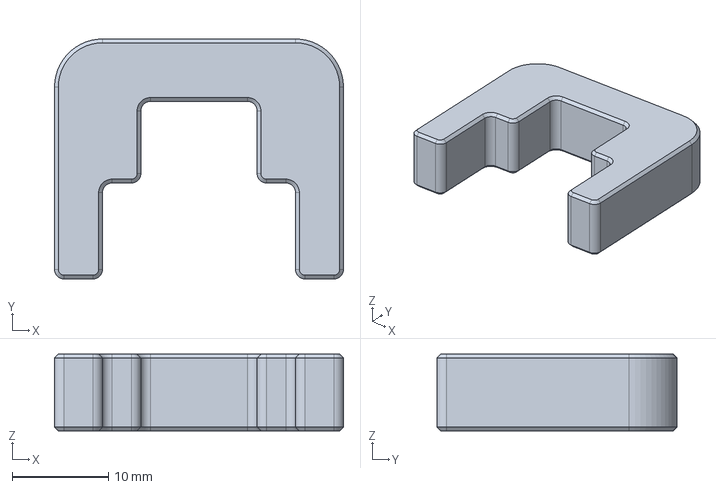
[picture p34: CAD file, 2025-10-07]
CAD/Tools/mgn12_rail_guide_x2.step
30.1 x 25.0 x 8.00 mm

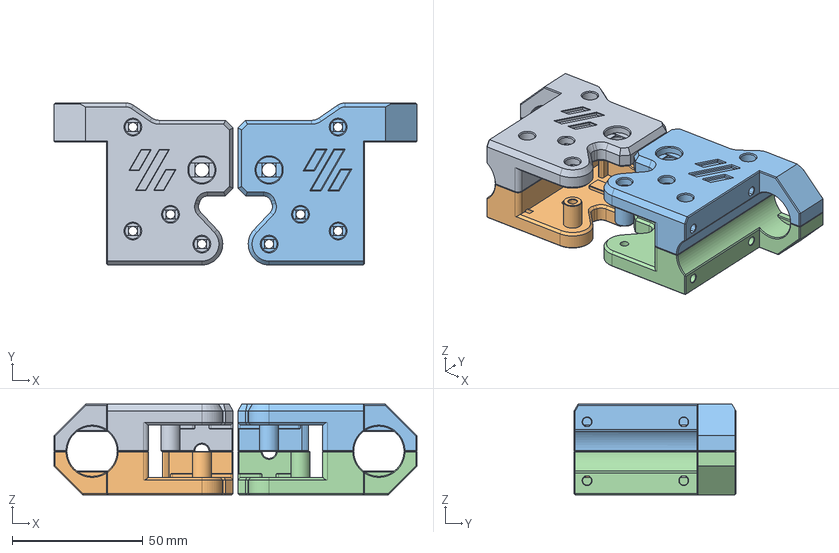
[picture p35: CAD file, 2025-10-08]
CAD/X_Gantry/[a]_xz_blocks.step
139.0 x 62.0 x 34.6 mm
[a]_x_block_front
[a]_x_block_rear
[a]_z_block_front
[a]_z_block_rear

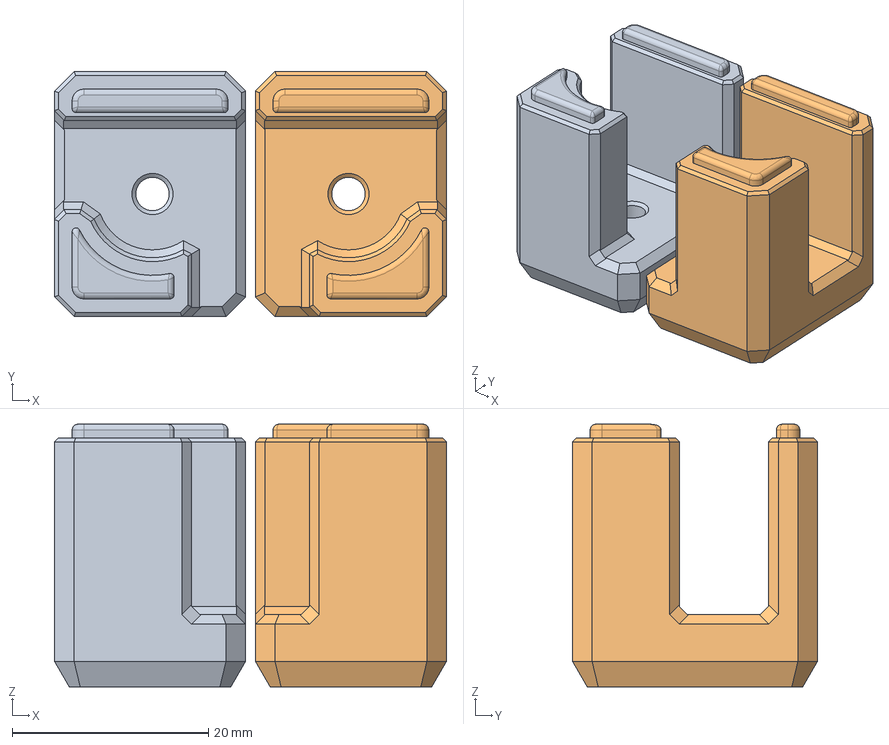
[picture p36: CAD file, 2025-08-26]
CAD/XZ_Axis/idler_block_b.step
40.0 x 25.0 x 26.8 mm

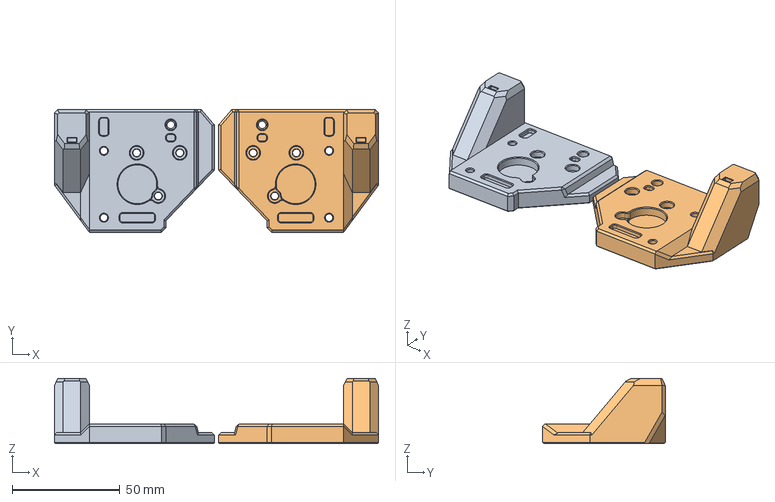
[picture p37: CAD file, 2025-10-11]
CAD/XZ_Axis/Motor Mount Primay Mounts by Rod Length and Diameter/10mm Rod Motor Mounts/motor_mounts_10mm_325mm.step
150.1 x 56.8 x 30.1 mm

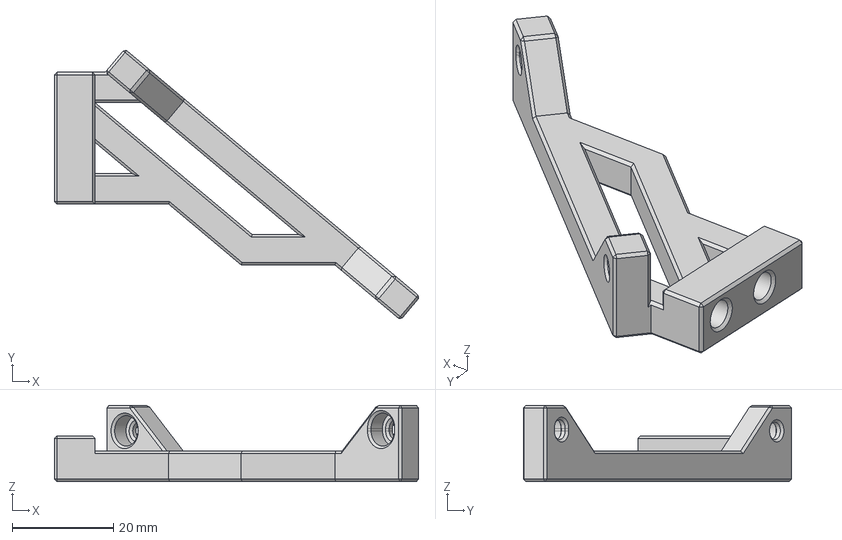
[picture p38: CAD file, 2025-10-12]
Mods/BTT HDMI 5 Mount/btt-hdmi-5-prusawire-mount.step
71.8 x 52.8 x 15.0 mm

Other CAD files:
CAD/XZ_Axis/Motor Mount Primay Mounts by Rod Length and Diameter/8mm Rod Motor Mounts/motor_mounts_8mm_325mm.step
Mods/BTT Pi TFT50 V2.1 Mount/front_grill_left.3mf
Mods/Cable Management/prusawire_psu_and_z-motor_cable_guide_top.3mf
Mods/Cable Management/STEP source files/prusawire_x_and_z-motor_cable_clips.step
CAD/Door_Puller/door_puller_anchor.f3d
CAD/Door_Puller/door_puller_anchor.step
CAD/Door_Puller/door_puller_bracket.f3d
CAD/Door_Puller/door_puller_bracket.step
CAD/Door_Puller/door_puller_idler_bracket.f3d
CAD/Electronics/black_psu_cover.f3d
CAD/Electronics/black_psu_cover.step
CAD/Electronics/btt_sb2209_usb_bracket.f3d
CAD/Electronics/btt_sb2209_usb_bracket.step
CAD/Electronics/daygreen_mosfet_bracket.f3d
CAD/Electronics/daygreen_mosfet_bracket.step
CAD/Electronics/heatbed_cable_clip.f3d
CAD/Electronics/heatbed_cable_clip.step
CAD/Electronics/mcu_box_einsy.f3d
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

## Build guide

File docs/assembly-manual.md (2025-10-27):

---
layout: default
title: "Assembly Manual"
nav_order: 5
---

# Assembly Manual

A Voron-style Assembly Manual / Build Guide is in the works.  Check back here soon for a released PDF!

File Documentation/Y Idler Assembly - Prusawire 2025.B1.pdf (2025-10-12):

## Y Axis Idler Bracket

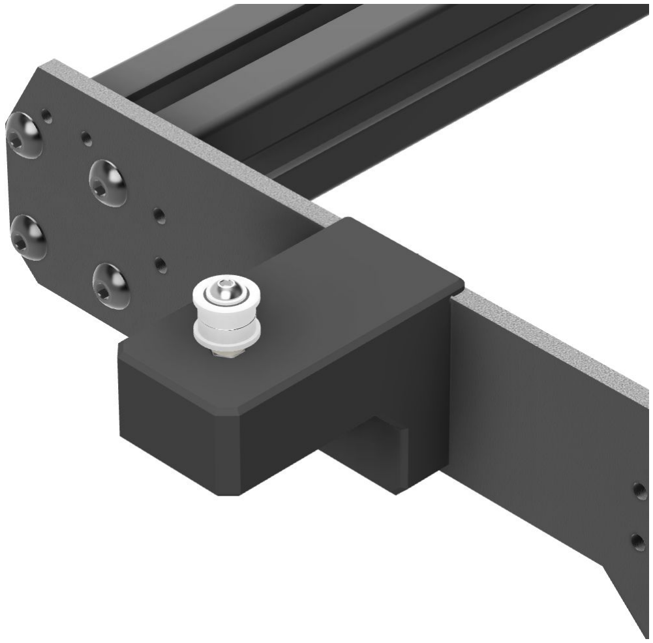
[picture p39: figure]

## Y Axis Idler Bracket

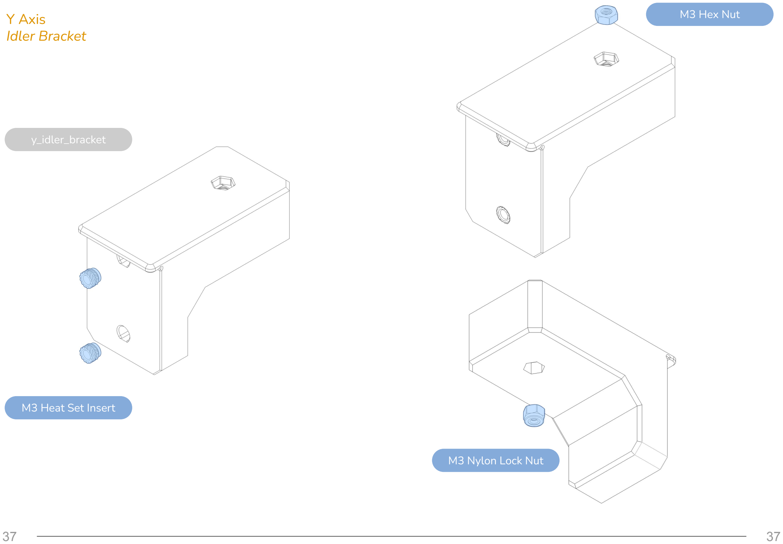
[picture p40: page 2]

### M3 Heat Set Insert

### M3 Hex Nut

### M3 Nylon Lock Nut

### y_idler_bracket

## Y Axis Idler Bracket

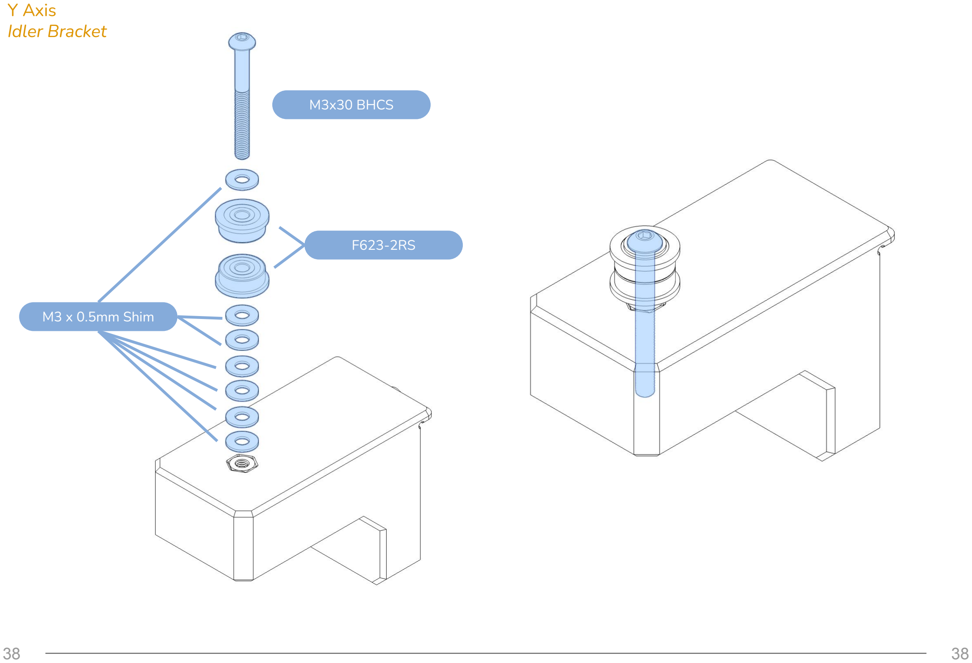
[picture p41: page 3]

### M3x30 BHCS

### M3 x 0.5mm Shim

### F623-2RS

## Y Axis Idler Bracket

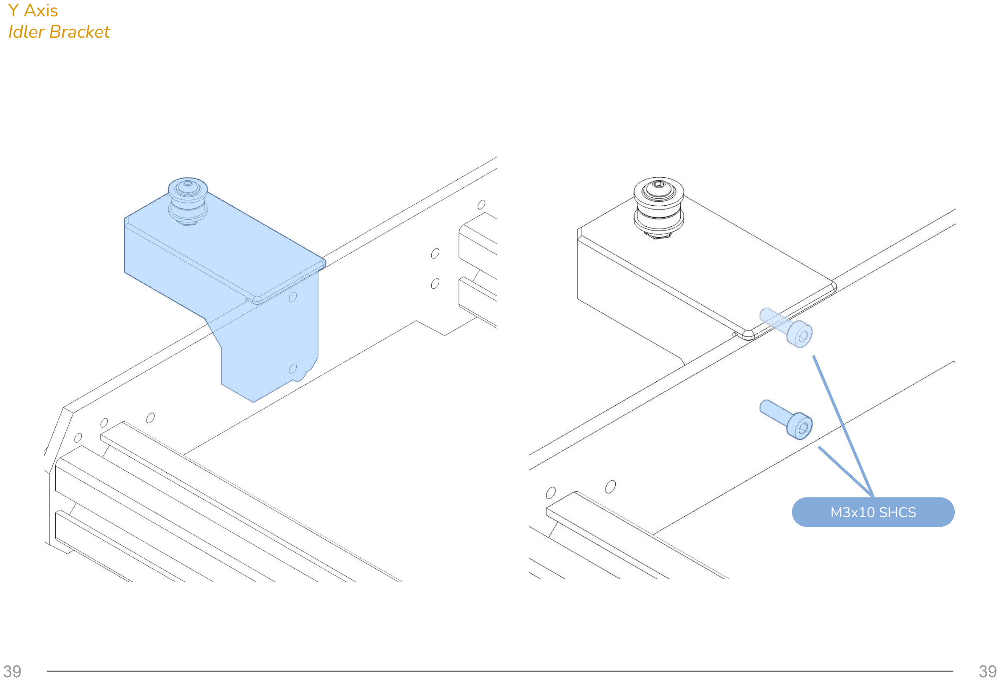
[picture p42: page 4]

### M3x10 SHCS

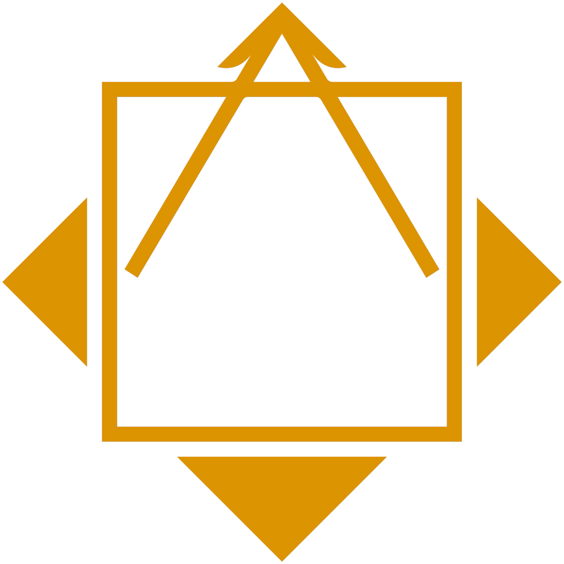
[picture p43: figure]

WEBSITE
https://www.positron3d.com/prusawire

GITHUB
https://github.com/Positron3D/Prusawire

DISCORD
https://discord.com/invite/positron

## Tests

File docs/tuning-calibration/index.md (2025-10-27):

---
layout: default
title: Tuning and Calibration Overview
has_children: true
nav_order: 8
---

# Tuning and Calibration Overview
{: .no_toc}

<details open markdown="block">
  <summary>
    Table of contents
  </summary>
  {: .text-delta }
- TOC
{:toc}
</details>

## General Resources
- Minimal 3DP's Basic Klipper Configuration Checks Procedure
	- [Klipper Basic Configuration Checks - Google Sheets](https://docs.google.com/spreadsheets/d/1CwccwL21RJTX0NQu1DDUu3yGtK1RVByJQGIV45AjyNA/edit?gid=0#gid=0)
- Minimal 3DP's Klipper Calibrations Spreadsheet
	- [Klipper Calibrations - Google Sheets](https://docs.google.com/spreadsheets/d/1LlSHsa86RuT_btswmDsmQp0LrTJ9U0HJcRhorsqz1ug/edit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)
	- This is extremely useful to dial in your hot end (e.g. if you're not using a Voron Revo, you're using something odd like the Bambu X1C Hotend, etc)
	- In particular:
		- Orca Slicer Flow Calibration
		- Orca Slicer Flow Calibration YOLO
		- Pressure Advance
		- PA & Orca Slicer
		- Max Volumetric Speed
		- Extrusion Rate Smoothing (ERS)
	- Nice to have:
		- Run Current
			- *particularly if using the BTT SKR Mini E3 V3.0 which can handle higher currents than the Einsey RAMbo...*
		- Skew Correction
- OrcaSlicer's Calibration Info: [Calibration · SoftFever/OrcaSlicer Wiki · GitHub](https://github.com/SoftFever/OrcaSlicer/wiki/Calibration)
- 

## Miscellaneous Notes
- Ella suggests that if using SKR Mini, motor currents can increase over the values provided for the slower Rambo board.  See Run Current above.

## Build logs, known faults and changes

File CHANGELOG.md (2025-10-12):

# Prusawire Change Log

Updated periodically to note significant design changes, fixes, and enhancements.

- 2025-10-11
    - y_idler_bracket replaced / updated with much stronger version. (via @erikbuild)
    - Added Rod Length Compatibility to motor mounts and idler brackets (via @Safe-ty)
        - Support 8mm rods: 320, 325, and 330mm lengths
        - Support 10mm rods: 320, 325, 330, and 341 lengths
        - Changed file structure to sort motor mounts by diameter
- 2025-10-07
    - Support for V0 Square Nuts for XZ Blocks, Y-Axis Parts (via @Safe-ty)
- 2025-10-06
    - Increase tolerance for 2020 Extrusion Length in XZ Blocks (via @Safe-ty)
        - Allow for 350 +2.0mm length
- 2025-08-26
    - Update idler blocks to eliminate belt rubbing (via @Ellafoxo)
- 2025-08-21
    - 2025.B1 "Beta 1" Released! (via @Ellafoxo)

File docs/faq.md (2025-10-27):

---
layout: default
title: "FAQ"
nav_order: 3
---

# Frequently Asked Questions

## Where is the latest BOM (Bill of Materials)?

The latest BOM can be [found on GitHub in the BOM folder](https://github.com/Positron3D/Prusawire/tree/main/BOM).

## How can I get a Serial # for my finished build?

We are accepting serials over on the [Positron 3D Discord](https://discord.com/invite/positron). Please submit your request to the `#prusawire-serial-request` channel over there.  There is an example submission and numerous other builds to reference for the format.

## Where can I get help with my build?

The community over on the [Positron 3D Discord](https://discord.com/invite/positron) is very helpful.  Check out the `#prusawire-questions` channel there.

## My NiteHawk-SB loses connection when there is a restart

If you are running V1.5 of the LDO Motors NiteHawh-SB USB board (the board that connects to the Raspberry Pi): you need to remove BOTH R6 and R7.

> the issue on NH-SB with a 1.5 USB board that looses communication after a "firmware restart" and needs a power cycle to turn back on is caused by the R7 and R6 resistor. They both need to be removed. There is a guide and video that shows how to remove the R7 here its the same for R6. If you are unable to or damage while trying reach out to your reseller where the kit was purchased and they will send you a replacement.
> @JoseFromLDO on the Voron Discord

[PDF Instruction Guide](assets/NiteHawkSB_R6-R7_Resistor_Removal_Guide.pdf): this details for R7, but you will ALSO need to remove R6!

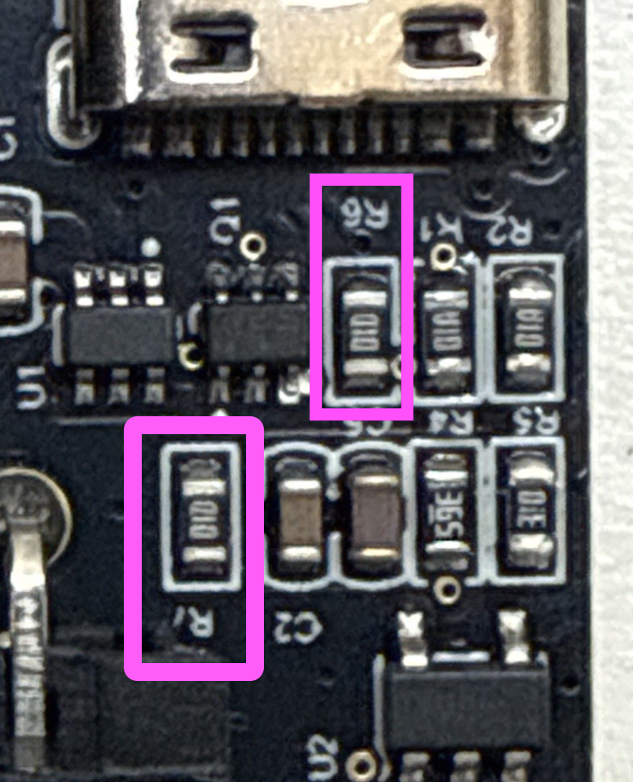
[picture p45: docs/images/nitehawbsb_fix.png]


## How do I make the cool silver serial sticker once I have my serial#?

Instructions from @Telefaksi (PW.0004):
>Custom serial sticker for Prusawire. Made for 24 mm tape, I used Brother TZe-M951 Black/Matt Silver tape. Included are Affinity Designer 2 package folder as .zip, .stl and .step files for printable cutting stencil. QR-code is made with Affinity Designer's QR-code tool so url can be edited to link to your serial request post. I exported .png image and imported it to Brother's P-touch Editor for printing.  
>Fonts are included in the package but in case you want to download them the fonts are from Google fonts. Play in regular and bold. https://fonts.google.com/specimen/Play
>In images folder is WEEE marking as vector image.

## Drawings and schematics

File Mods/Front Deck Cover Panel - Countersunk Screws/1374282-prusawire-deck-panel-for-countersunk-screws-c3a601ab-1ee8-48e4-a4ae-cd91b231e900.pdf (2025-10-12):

## Prusawire Deck Panel for

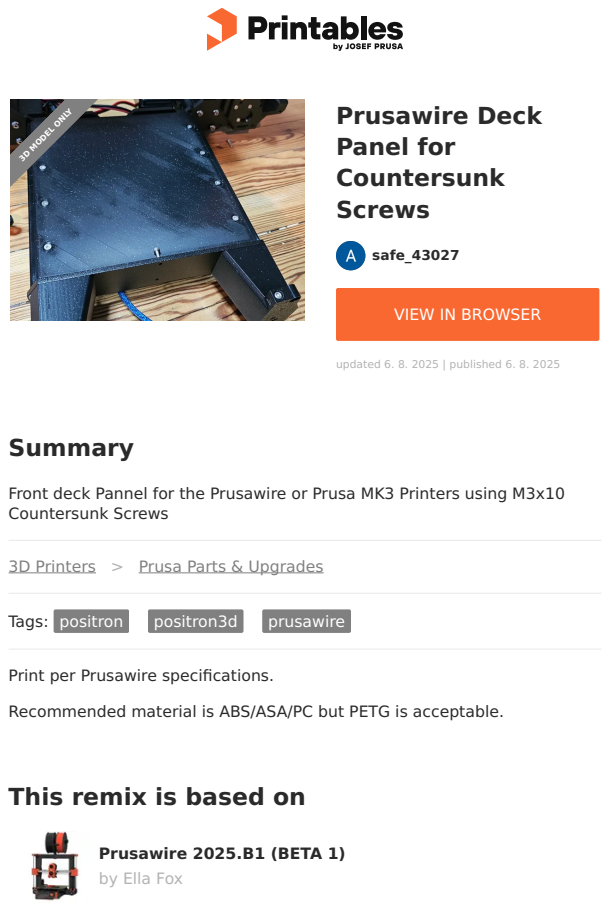
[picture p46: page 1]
Summary; Tags:; positron; positron3d; prusawire; safe_43027; Countersunk Screws; updated 6. 8. 2025 | published 6. 8. 2025; 3D MODEL ONLY

VIEW IN BROWSER (https://printables.com/model/1374282-prusawire-deck-panel-for-countersunk-screws)

Front deck Pannel for the Prusawire or Prusa MK3 Printers using M3x10
Countersunk Screws

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

Print per Prusawire specifications.

Recommended material is ABS/ASA/PC but PETG is acceptable.

This remix is based on

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

## Model files

## License

This work is licensed under a GNU

General Public License v3.0 (https://www.gnu.org/licenses/gpl-3.0.html)

✖ | Sharing without ATTRIBUTION
✔ | Remix Culture allowed
✔ | Commercial Use
✔ | Meets Open Definition
ℹ | Share under the same license deck_panel_front_m3_countersunk_screws.stl

deck_panel_front_m3_countersunk_screws.step

deck_panel_front_m3_countersunk_screws.f3d

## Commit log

2025-07-27 Backfill 2025.B1 release.
    [8mm_bearing_adapter_x2.f3d, 8mm_bearing_adapter_x2.step, [a]_8mm_bearing_adapter_x2.stl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]
2025-08-26 Backfill updated idler blocks.
    [idler_block_b.f3d, idler_block_b.step, x_idler_block_b.stl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]
2025-10-07 Fixed Symmetry Issue on mgn12 rail guide
    Fixed 3 files.
    hI nexus$
    [mgn12_rail_guide_x2.f3d, mgn12_rail_guide_x2.step, mgn12_rail_guide_x2.stl]
2025-10-07 Increase tolerance for XZ blocks
    Allow for 350 +2 max tolerance for extrusion length
    [[a]_x_block_front.stl, [a]_x_block_rear.stl, [a]_xz_blocks.f3d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]
2025-10-08 Include modifications for V0 Square Nuts
    Hi Kris, this is all your fault. Why you only stock V0 square nuts and not the Prusa stock M3n Slim?
    [[a]_x_block_front.stl, [a]_x_block_rear.stl, [a]_xz_blocks.f3d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]
2025-10-08 Square Nut Fix Part 2
    Modifications to the y-axis parts to allow use of V0 sized square nuts. Cause they dare to be different.
    [y_belt_tensioner_rear.f3d, y_belt_tensioner_rear.step, y_belt_tensioner_rear.stl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]
2025-10-11 Extraction and cleanup of Beta 1 BOM from Google Sheets (#25)
    * Added quick listing of popular mods.
    * Added 2025.Beta1 BOM.
    * Tweaks to BOM formatting.
2025-10-11 Update BOM_2025-B1.md
    Updated square nut count and heat press insert count.
    Square nut count is 12 +2 extra
    Heat insert is 100 for spares
2025-10-11 Added Rod Length Compatibility
    Changed file structure to sort motor mounts by diameter.
    Added compatibility for the following rod and length combinations:
    8mm rods: 320, 325, and 330mm lengths
    10mm rods: 320, 325, 330, and 341 lengths
    [[a]_idler_block_10mm.f3d, [a]_idler_block_10mm.step, [a]_idler_block_8mm.f3d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]
2025-10-12 Backfill popular mods. (#28)
    Thanks to @erikbuild, all tagged mods have been added to the github.
    To add a mod, simply submit a pull request and it shall be added. :)
    [btt-hdmi-5-prusawire-mount.f3d, btt-hdmi-5-prusawire-mount.step, btt-hdmi-5-prusawire-mount.stl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]
2025-10-12 Y Idler - Harder Better Faster Stronger (#29)
    * Added Y-Idler assembly PDF.
    * Added erikbuild super strong y_idler assembly.
    * Minor tweaks and link additions to README.
    * Replace y_idler_bracket with erikbuild super strong remix.
    [Y Idler Assembly.f3d, Y Idler Assembly.step, y_idler_bracket.f3d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]
2025-10-12 Add initial OrcaSlicer presets to enable easier fine tuning of Pressure Advance, etc. (#30)
